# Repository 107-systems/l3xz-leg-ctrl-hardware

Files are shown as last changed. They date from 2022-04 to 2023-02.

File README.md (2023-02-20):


`l3xz-leg-ctrl-hardware`
========================


Custom leg controller board for the [L3X-Z Hexapod](https://github.com/107-systems/l3xz-hw).

<p align="center">
  
</p>

## Firmware
[l3xz-leg-ctrl-firmware](https://github.com/107-systems/l3xz-leg-ctrl-firmware)

## Pin Usage
### Arduino Nano 33 IoT connector CN1
| **Pin** | **Pin Name** | **Signal** | **Description** |
|:---:|:---:|:---:|:---:|
| 1 | D13/SCK | SPI_SCK | SPI for CAN and AS5048 encoder |
| 2 | +3V3 | 3V3-rail | supply voltage for board |
| 3 | AREF | | |
| 4 | DAC0/A0 | | |
| 5 | A1 | +BATT_MEAS | measurement of input voltage |
| 6 | A2 | | |
| 7 | A3 | | |
| 8 | A4/SDA | I2C_SDA | I2C for eeprom and qwiic |
| 9 | A5/SCL | I2C_SCL | I2C for eeprom and qwiic |
| 10 | A6 | LED3 | status LED 3 |
| 11 | A7 | LED2 | status LED 2 |
| 12 | VUSB/+5V0 | | |
| 13 | REC/RESET | RESET | Reset |
| 14 | GND | GND | GND |
| 15 | VIN | power input | power input for board |
| 16 | D1/TX | SERIAL_TX | to connector CN3 |
| 17 | D0/RX | SERIAL_RX | to connector CN3 |
| 18 | RESET | RESET | Reset |
| 19 | GND | GND | GND |
| 20 | D2 | LED1 | status LED 1 |
| 21 | D3 | MCP2515_CS | chip select for CAN |
| 22 | D4 | AS5048_1_CS | chip select for AS5048 1 |
| 23 | D5 | AS5048_2_CS | chip select for AS5048 2 |
| 24 | D6 | BUMPER | input for bumper |
| 25 | D7 | SERVO1 | PWM output for servo 1 |
| 26 | D8 | | |
| 27 | D9 | MCP2515_INT | CAN interrupt |
| 28 | D10 | SERVO2 | PWM output for servo 2 |
| 29 | D11/MOSI | SPI_MOSI | SPI for CAN and AS5048 encoder |
| 30 | D12/MISO | SPI_MISO | SPI for CAN and AS5048 encoder |

### Qwiic I2C connector CN2
JST SH 1mm 4-pin.

| **Pin** | **Signal** |
|:---:|:---:|
| 1 | GND |
| 2 | VCC |
| 3 | I2C_SDA |
| 4 | I2C_SCL |

### Serial connector CN3
JST SH 1mm 4-pin.

| **Pin** | **Signal** |
|:---:|:---:|
| 1 | GND |
| 2 | VCC |
| 3 | SERIAL_TX |
| 4 | SERIAL_RX |

### Dronecode CAN connector CN4 and CN5
JST GH 1.25mm 4-pin.

| **Pin** | **Signal** |
|:---:|:---:|
| 1 | CANVCC |
| 2 | CANH |
| 3 | CANL |
| 4 | GND |

### Power Input CN6
Würth WR-TBL 3.81mm 2-pin.

| **Pin** | **Signal** | **Description** |
|:---:|:---:|:---:|
| 1 | V-IN | Directly to Arduino Nano VIN |
| 2 | GND | |

Attention: V_IN is 5 to 21 V and is directly connected to VIN of the Arduino with a diode for reverse polarity protection.
It is also directly connected to +5V of the servo connector. So it should be limited to +6V if servos are used.

### Cervo connector CN7
2x3 pin-header 2.54 mm.

| **Pin** | **Signal** | **Description** |
|:---:|:---:|:---:|
| 1+2 | servo-pwm | 50 Hz pulse signal |
| 3+4 | +5V | directly connected to VIN |
| 5+6 | GND | |

### Bumper Connector CN8
WAGO 733-362 2.5mm 2-pin.

| **Pin** | **Signal** | **Description** |
|:---:|:---:|:---:|
| 1 | BUMPER | 10k pull up to +3.3V |
| 2 | GND | |

## BOM

| **Designator** | **Part Name** | **Link** |
|:---:|:---:|:---:|
| C1, C2, C3, C4, C5, C6, C9 | Capacitor 0603 100nF 25V  | |
| C7, C8 | do not install | |
| C10, C11 | do not install | |
| CN1 | Arduino Nano | https://www.reichelt.de/praez-buchsenleisten-2-54-mm-1x15-gerade-mpe-115-1-015-p187279.html |
| CN2, CN3 | JST SH SM04B-SRSS-TB | |
| CN4, CN5 | JST GH SM04B-GHS-TB | https://www.voelkner.de/products/1102742/JST-Stiftgehaeuse-Platine-GH-Polzahl-Gesamt-4-Rastermass-1.25mm-SM04B-GHS-TB-LF-SN.html |
| CN6 | Würth WR-TBL 691322310002 | |
| CN7 | Pinheader 2.54 mm 2x3 | https://www.reichelt.de/stiftleisten-2-54-mm-2x03-gewinkelt-mpe-088-2-006-p119904.html |
| CN8 | WAGO 733-362 | https://www.reichelt.de/print-stiftleiste-micro-rm-2-5-gewinkelt-2-pol--wago-733-362-p45863.html |
| D1 | LED 0603 green | https://www.reichelt.de/led-smd-1608-0603-gruen-112-mcd-120--led-el-0603-gr1-p156254.html |
| D2, D3 | MBR0530T1G | https://www.reichelt.de/schottkydiode-30-v-0-5-a-sod-123-mbr0530t1g-ons-p219621.html |
| D4 | LED 0603 yellow | https://www.reichelt.de/led-smd-1608-0603-gelb-180-mcd-120--led-el-0603-ge-p156259.html |
| D5 | LED 0603 red | https://www.reichelt.de/led-smd-1608-0603-rot-180-mcd-120--led-el-0603-rt-p156256.html |
| R1, R2, R3, R4, R6, R7, R8, R9, R10, R14 | Resistor 0603 10k | |
| R5, R15, R16 | Resistor 0603 3k3 | |
| R11, 12 | do not install | |
| R13 | Resistor 0603 100k | |
| U1, U2 | AS5048A | |
| U3 | 24LC64-I/SN | https://www.reichelt.de/eeprom-seriell-64-kb-8-k-x-8-i2c-2-5--5-5-v-so-8-24lc64-i-sn-p40079.html |
| U4 | MCP2515-I/P DIP-18 | https://www.reichelt.de/can-controller-mit-spi-schnittstelle-dil-18-mcp-2515-i-p-p54514.html |
| U8 alternative | MCP2515-I/SO SO-18 | https://www.reichelt.de/can-controller-mit-spi-schnittstelle-2-7--5-5-v-so-18-mcp-2515-i-so-p54515.html |
| U9 | SN65HVD232D | |
| U9 alternative | SN65HVD230D | https://www.reichelt.de/high-speed-can-transceiver-1-mbit-s-3-3-v-so-8-sn-65hvd230d-p58427.html |
| Y1 | Quartz 16 MHz 5x2.5mm | https://www.reichelt.de/keramik-smd-quarz-3x5x1mm-16-0mhz-16-000000-mj-p85005.html |

## PCB
### Top
<p align="center">
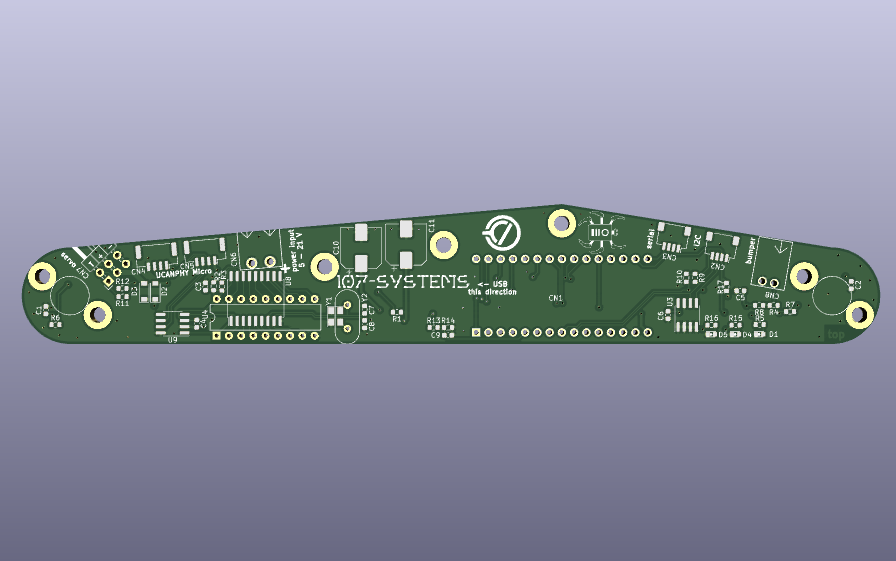
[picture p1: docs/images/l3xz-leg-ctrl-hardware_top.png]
  </a>
</p>
### Bottom
<p align="center">
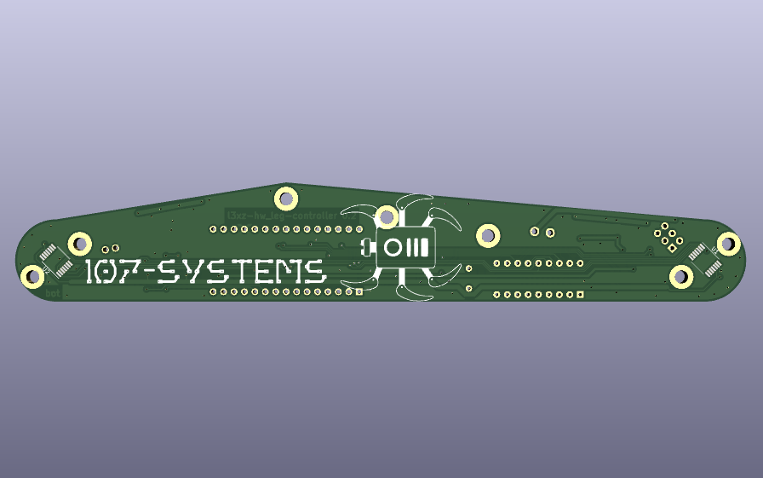
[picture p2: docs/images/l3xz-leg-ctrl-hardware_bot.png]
  </a>
</p>

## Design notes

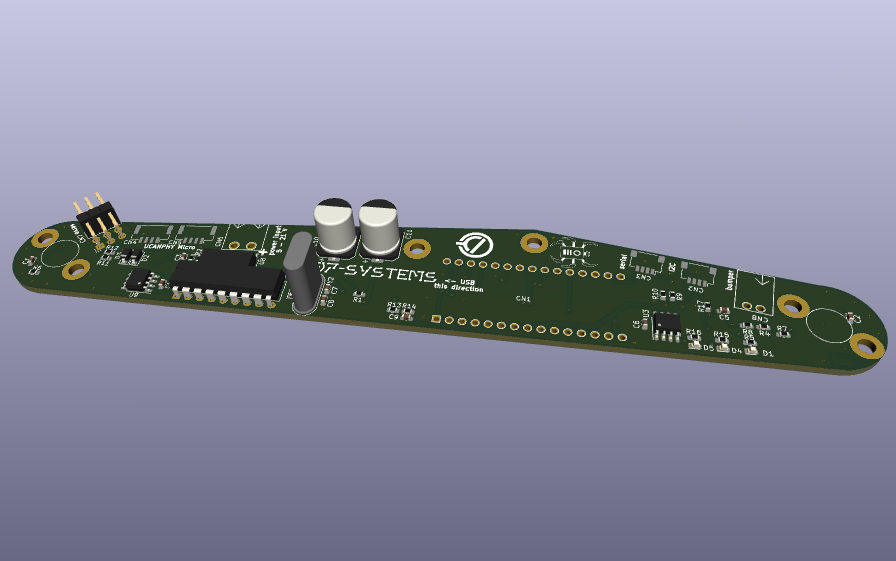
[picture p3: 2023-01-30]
docs/images/l3xz-leg-ctrl-hardware_rendering.png

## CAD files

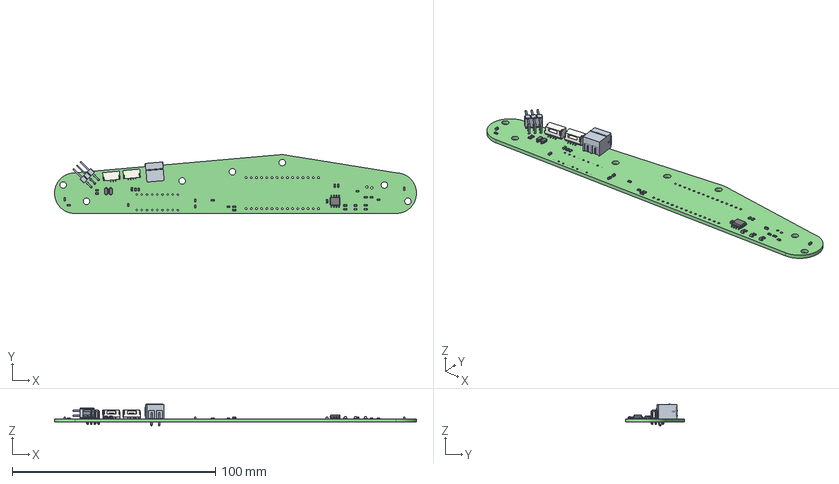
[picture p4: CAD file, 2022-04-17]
l3xz-leg-ctrl-hardware.step
178.0 x 29.0 x 10.7 mm
SOIC-18_7.5x11.6mm_Pitch1.27mm
SOIJ-8_5.3x5.3mm_Pitch1.27mm
c_elec_8x10 x 2

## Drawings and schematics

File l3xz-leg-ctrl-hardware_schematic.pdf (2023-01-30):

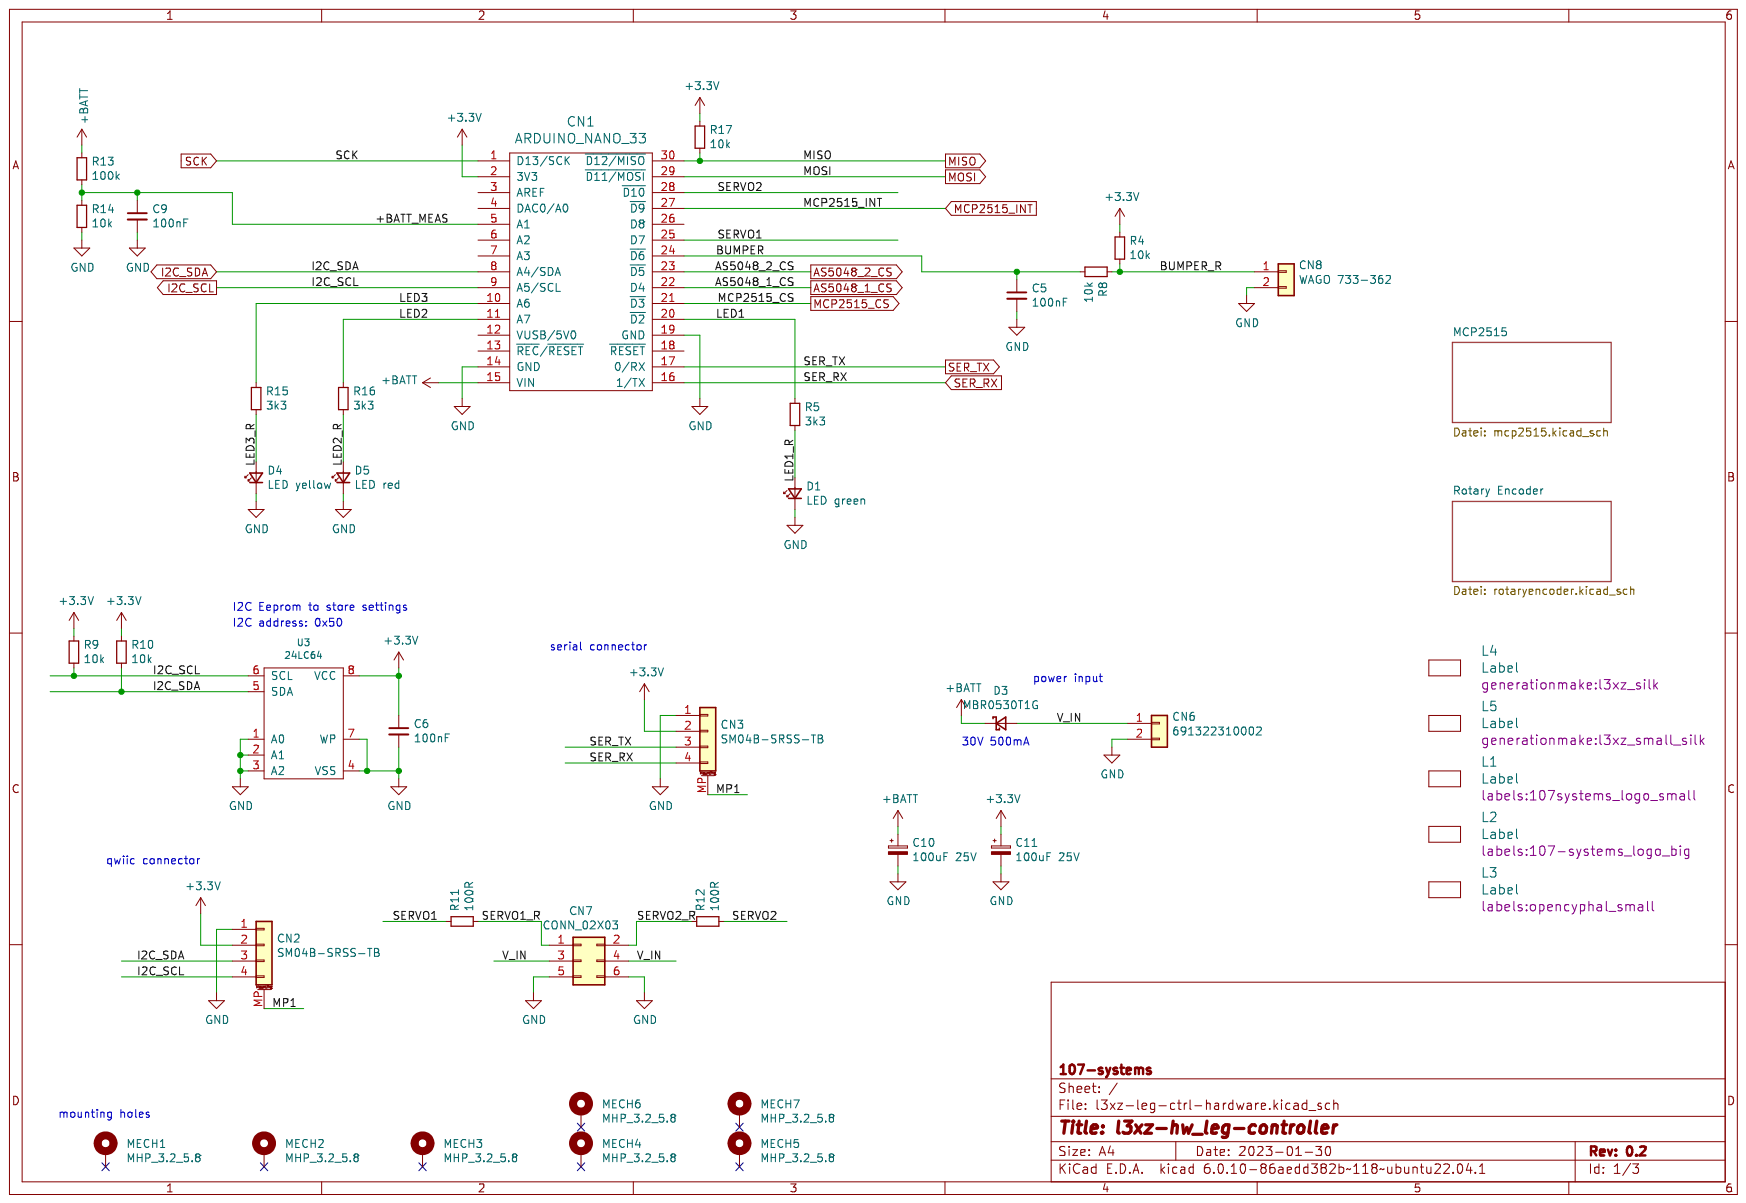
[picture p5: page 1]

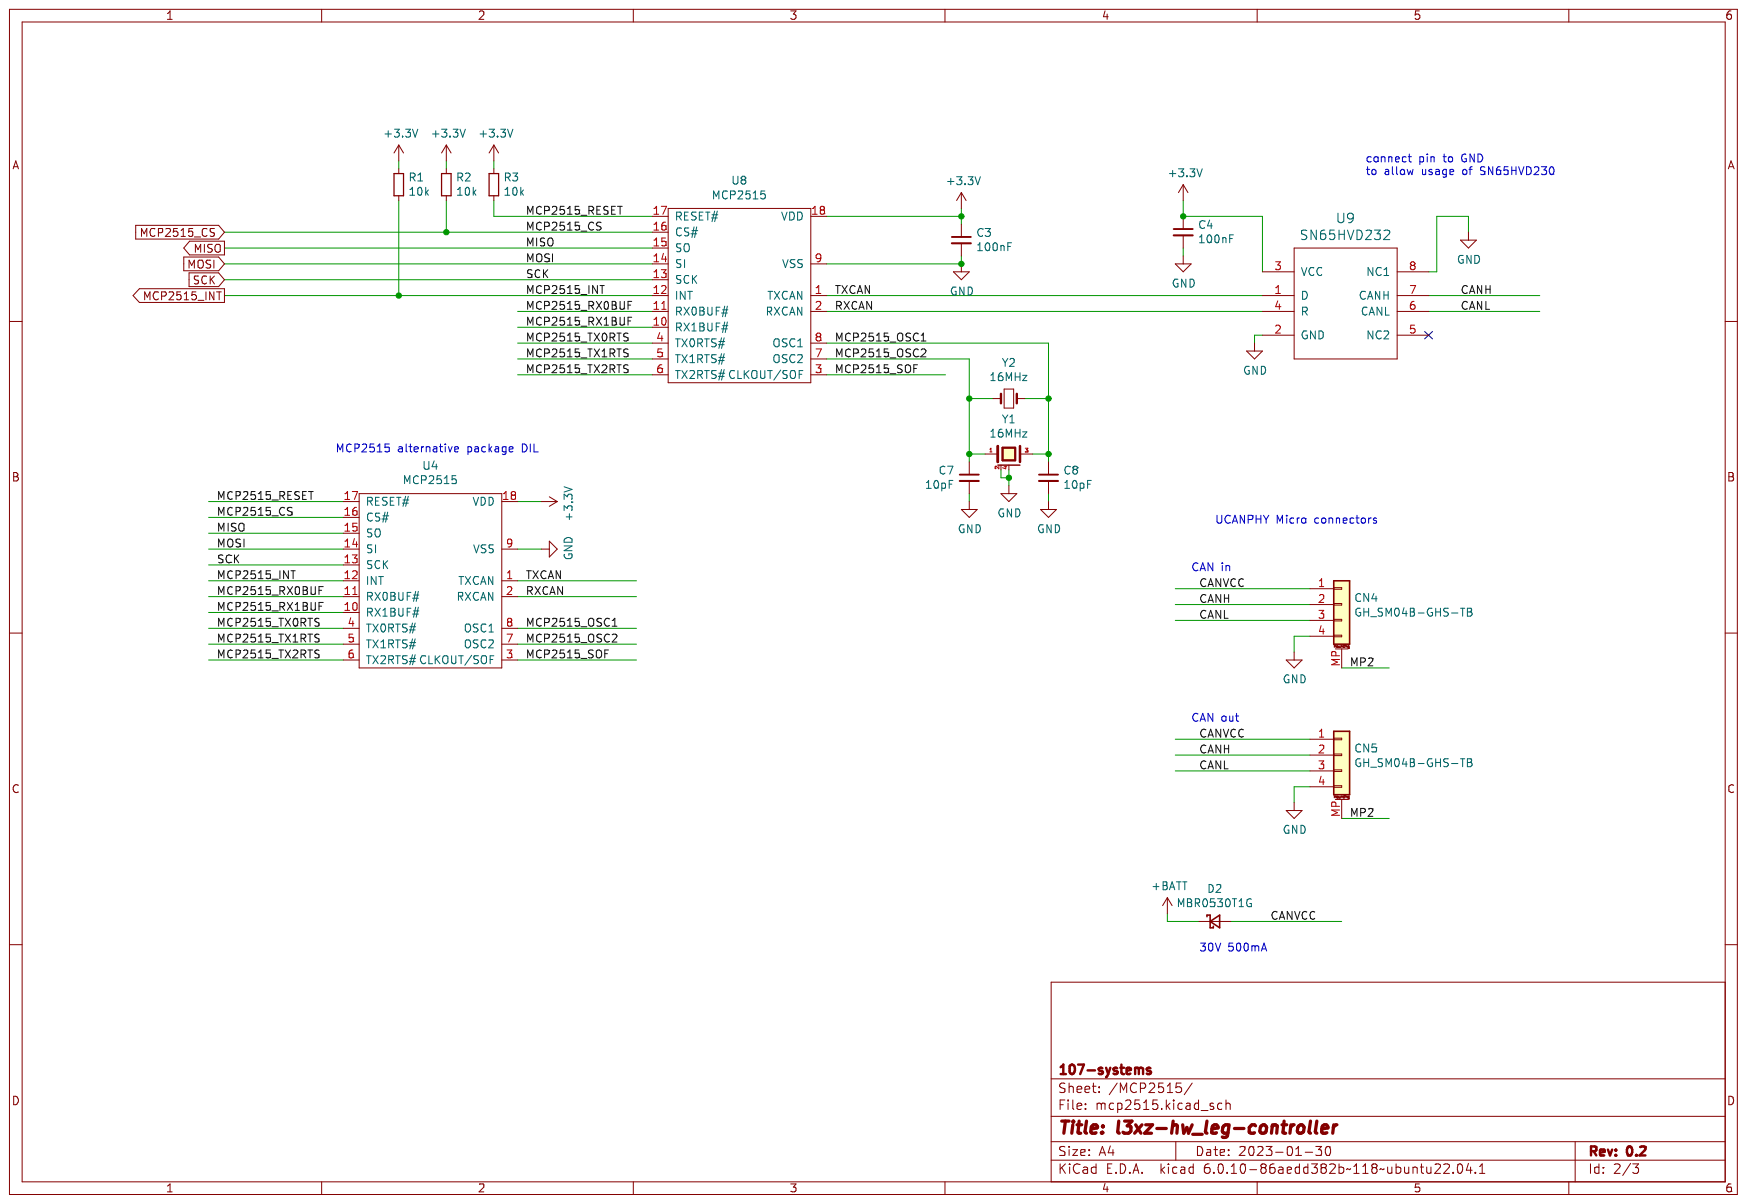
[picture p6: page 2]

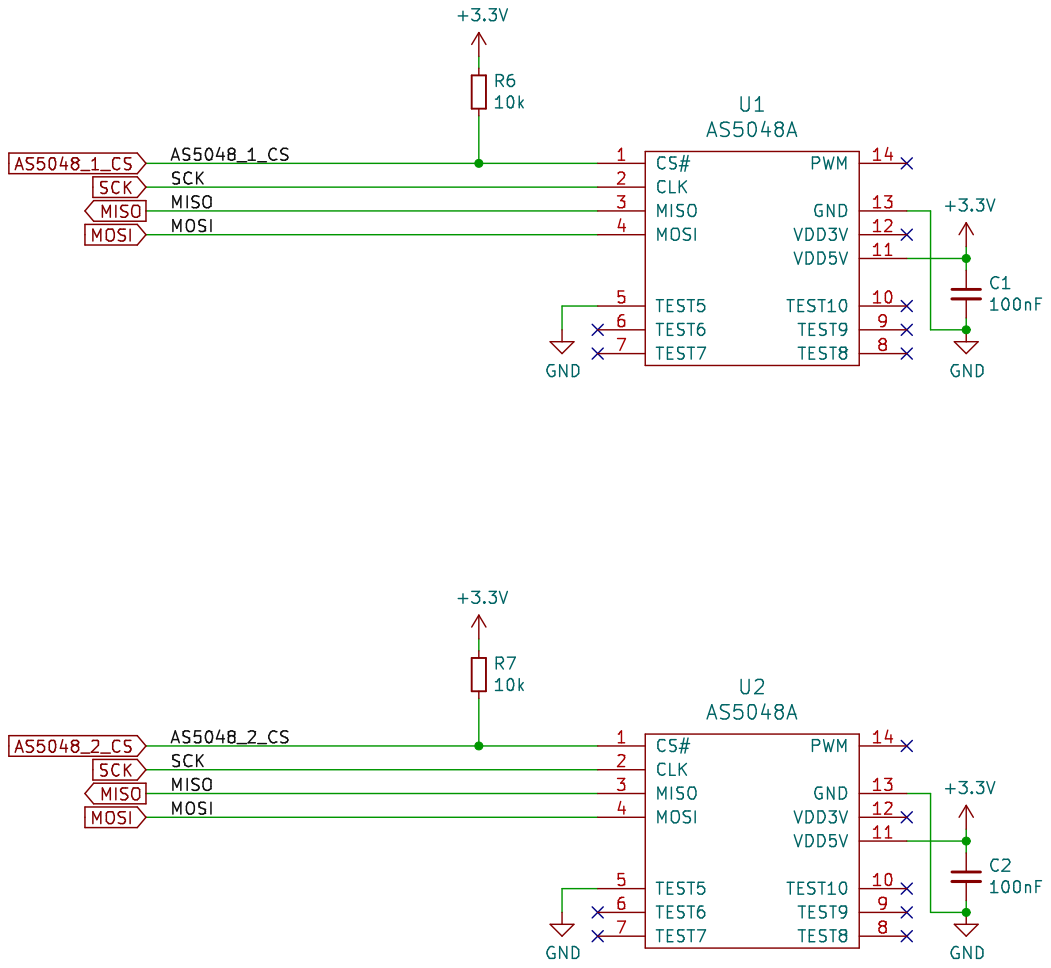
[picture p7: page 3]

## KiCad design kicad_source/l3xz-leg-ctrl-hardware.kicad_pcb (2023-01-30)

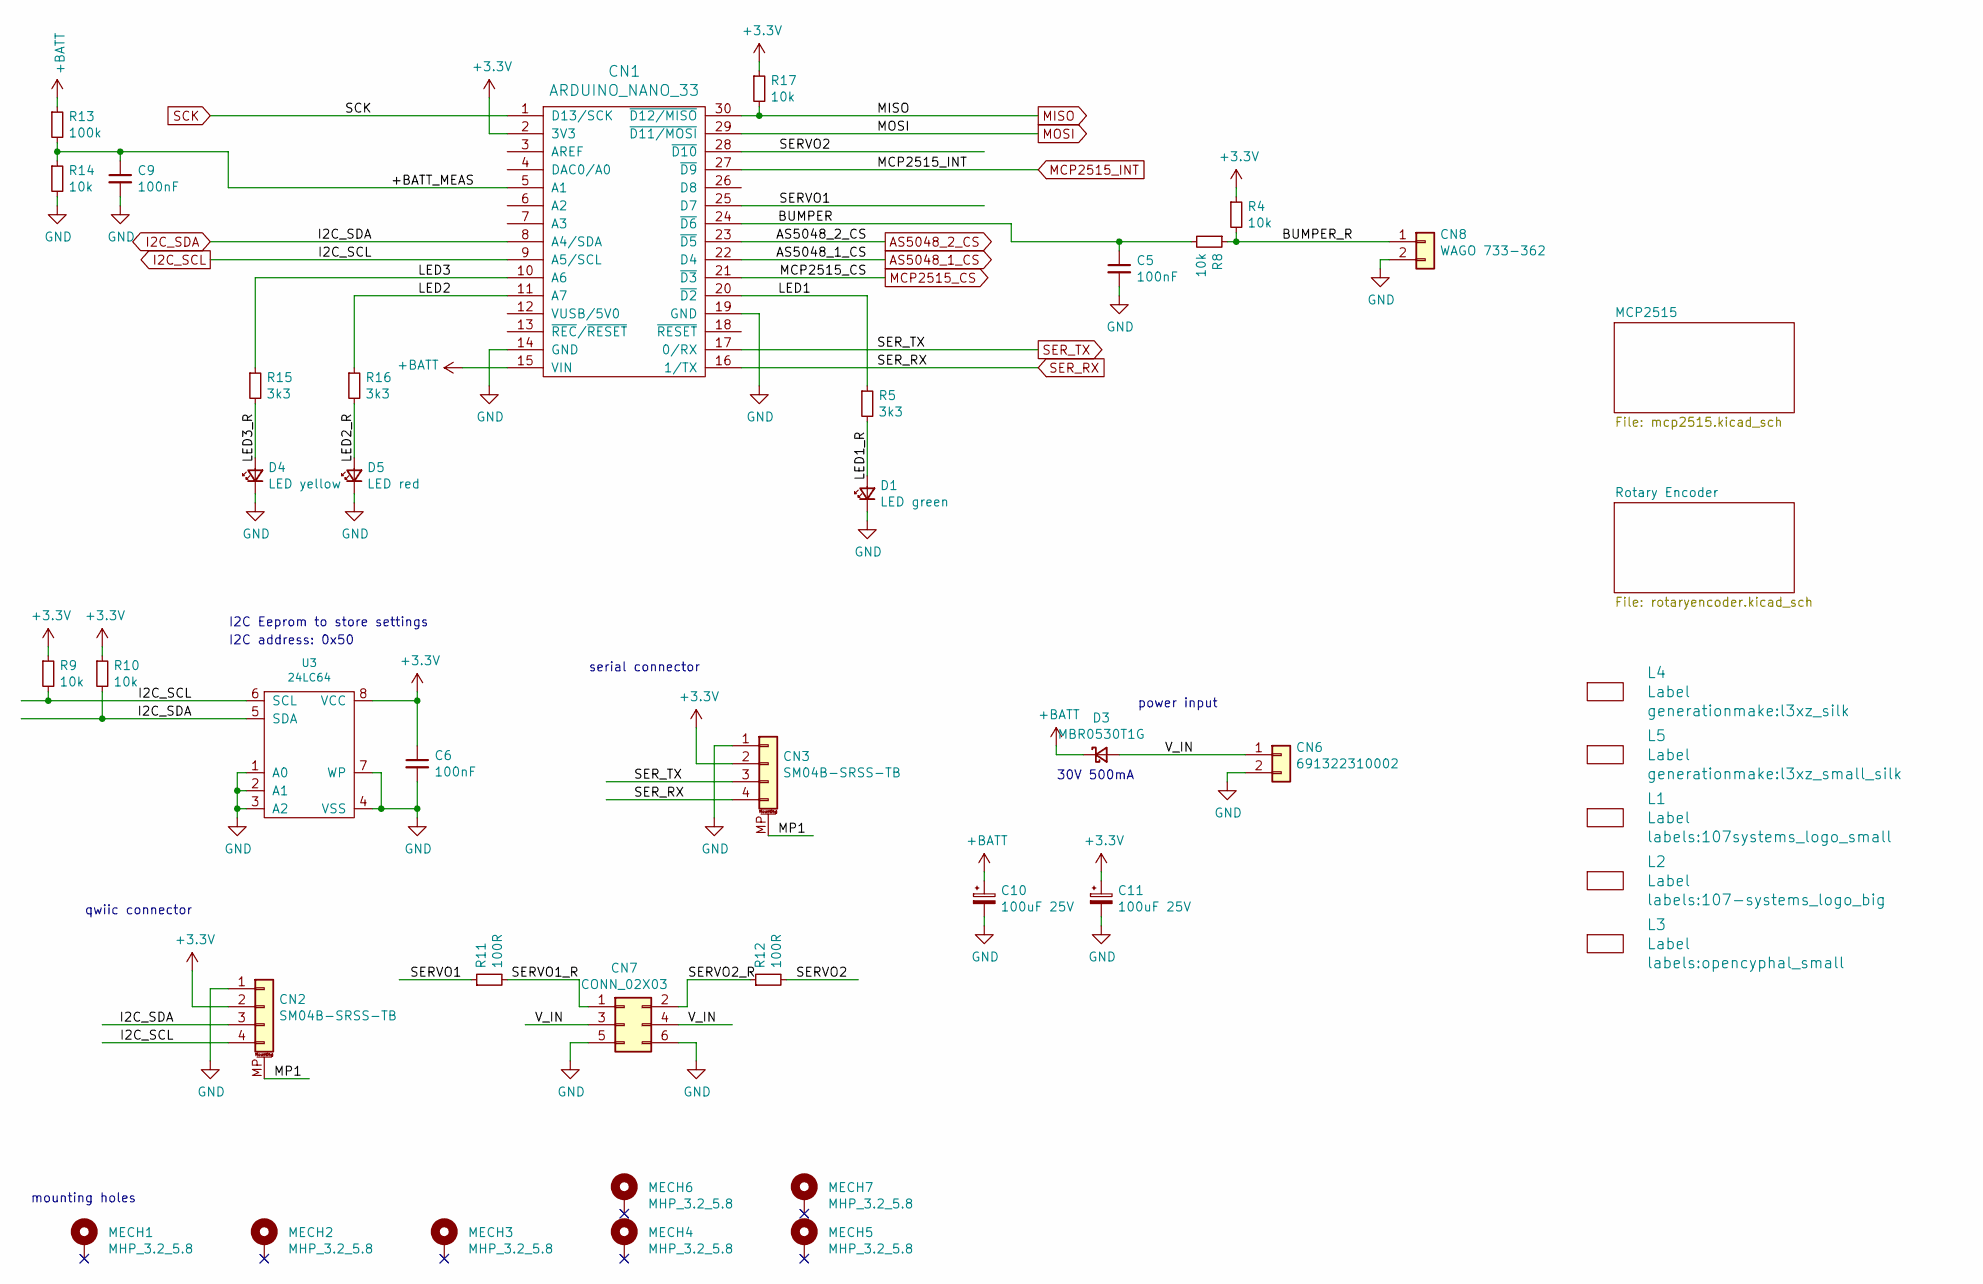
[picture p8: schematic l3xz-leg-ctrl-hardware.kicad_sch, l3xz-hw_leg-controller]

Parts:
C5, C6, C9: 100nF; C_0603_1608Metric
C10, C11: 100uF 25V; CP_Elec_8x10
CN1: ARDUINO_NANO_33
CN2, CN3: SM04B-SRSS-TB; JST_SH_SM04B-SRSS-TB_1x04-1MP_P1.00mm_Horizontal
CN6: 691322310002; WR-TBL_691322310002
CN7: CONN_02X03; PinHeader_2x03_P2.54mm_Horizontal
CN8: WAGO 733-362; WR-TBL_691382010002
D1: LED green; LED_0603
D3: MBR0530T1G; D_SOD-123
D4: LED yellow; LED_0603
D5: LED red; LED_0603
L1: Label; 107systems_logo_small
L2: Label; 107-systems_logo_big
L3: Label; opencyphal_small
L4: Label; l3xz_silk
L5: Label; l3xz_small_silk
MECH1, MECH2, MECH3, MECH4, MECH5, MECH6, MECH7: MHP_3.2_5.8
R4, R8, R9, R10, R14, R17: 10k; R_0603_1608Metric
R5, R15, R16: 3k3; R_0603_1608Metric
R11, R12: 100R; R_0603_1608Metric
R13: 100k; R_0603_1608Metric
U3: 24LC64; SOIC-8_3.9x4.9mm_P1.27mm

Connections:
+3.3V: C6.1, C11.1, CN1.2 (3V3), CN2.2, CN3.2, R4.1, R9.1, R10.1, R17.1, U3.8 (VCC); also elsewhere on the board
+BATT: C10.1, CN1.15 (VIN), D3.1 (K), R13.1; also elsewhere on the board
/+BATT_MEAS: C9.1, CN1.5 (A1), R13.2, R14.1
/BUMPER: C5.1, CN1.24 (~D6), R8.2
/BUMPER_R: CN8.1, R4.2, R8.1
/LED1: CN1.20 (~D2), R5.1
/LED1_R: D1.2 (A), R5.2
/LED2: CN1.11 (A7), R16.1
/LED2_R: D5.2 (A), R16.2
/LED3: CN1.10 (A6), R15.1
/LED3_R: D4.2 (A), R15.2
/MP1: CN2.MP (MountPin), CN3.MP (MountPin)
/SERVO1: CN1.25 (D7), R11.1
/SERVO1_R: CN7.1, R11.2
/SERVO2: CN1.28 (~D10), R12.2
/SERVO2_R: CN7.2, R12.1
/V_IN: CN6.1, CN7.3, CN7.4, D3.2 (A)
AS5048_1_CS: CN1.22 (D4); also elsewhere on the board
AS5048_2_CS: CN1.23 (~D5); also elsewhere on the board
GND: C5.2, C6.2, C9.2, C10.2, C11.2, CN1.14 (GND), CN1.19 (GND), CN2.1, CN3.1, CN6.2, CN7.5, CN7.6, CN8.2, D1.1 (K), D4.1 (K), D5.1 (K), R14.2, U3.1 (A0), U3.2 (A1), U3.3 (A2), U3.4 (VSS), U3.7 (WP); also elsewhere on the board
I2C_SCL: CN1.9 (A5/SCL), CN2.4, R9.2, U3.6 (SCL)
I2C_SDA: CN1.8 (A4/SDA), CN2.3, R10.2, U3.5 (SDA)
MCP2515_CS: CN1.21 (~D3); also elsewhere on the board
MCP2515_INT: CN1.27 (~D9); also elsewhere on the board
MISO: CN1.30 (~D12/MISO), R17.2; also elsewhere on the board
MOSI: CN1.29 (~D11/MOSI); also elsewhere on the board
SCK: CN1.1 (D13/SCK); also elsewhere on the board
SER_RX: CN1.16 (1/TX), CN3.4
SER_TX: CN1.17 (0/RX), CN3.3

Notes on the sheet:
serial connector
power input
I2C address: 0x50
qwiic connector
mounting holes
30V 500mA
I2C Eeprom to store settings

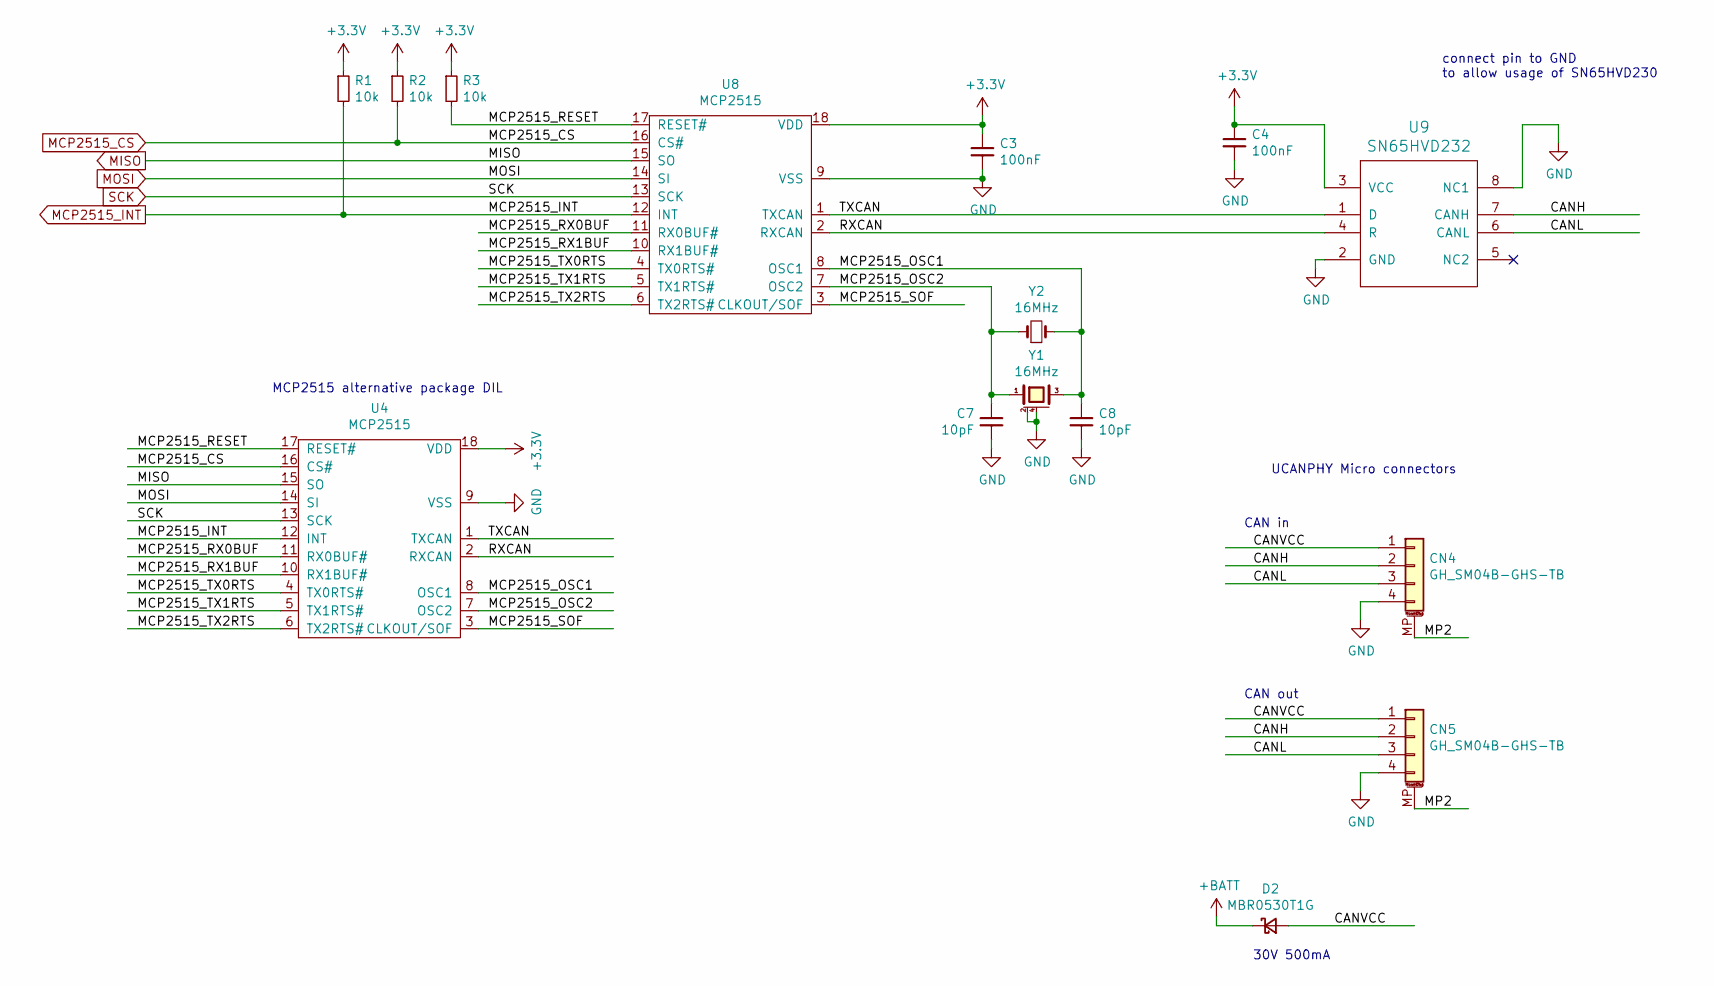
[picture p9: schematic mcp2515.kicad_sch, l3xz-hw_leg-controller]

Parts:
C3, C4: 100nF; C_0603_1608Metric
C7, C8: 10pF; C_0603_1608Metric
CN4, CN5: GH_SM04B-GHS-TB; JST_GH_SM04B-GHS-TB_1x04-1MP_P1.25mm_Horizontal
D2: MBR0530T1G; D_SOD-123
R1, R2, R3: 10k; R_0603_1608Metric
U4: MCP2515; DIP-18_W7.62mm
U8: MCP2515; SOIC-18W_7.5x11.6mm_P1.27mm
U9: SN65HVD232; SOIC-8_3.9x4.9mm_P1.27mm
Y1: 16MHz; Crystal_SMD_SeikoEpson_FA238V-4Pin_3.2x2.5mm
Y2: 16MHz; Crystal_HC49-U_Vertical

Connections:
+3.3V: C3.1, C4.1, R1.1, R2.1, R3.1, U4.18 (VDD), U8.18 (VDD), U9.3 (VCC); also elsewhere on the board
+BATT: D2.1 (K); also elsewhere on the board
/MCP2515/CANH: CN4.2, CN5.2, U9.7 (CANH)
/MCP2515/CANL: CN4.3, CN5.3, U9.6 (CANL)
/MCP2515/CANVCC: CN4.1, CN5.1, D2.2 (A)
/MCP2515/MCP2515_OSC1: C8.1, U4.8 (OSC1), U8.8 (OSC1), Y1.3, Y2.2
/MCP2515/MCP2515_OSC2: C7.1, U4.7 (OSC2), U8.7 (OSC2), Y1.1, Y2.1
/MCP2515/MCP2515_RESET: R3.2, U4.17 (RESET#), U8.17 (RESET#)
/MCP2515/MCP2515_RX0BUF: U4.11 (RX0BUF#), U8.11 (RX0BUF#)
/MCP2515/MCP2515_RX1BUF: U4.10 (RX1BUF#), U8.10 (RX1BUF#)
/MCP2515/MCP2515_SOF: U4.3 (CLKOUT/SOF), U8.3 (CLKOUT/SOF)
/MCP2515/MCP2515_TX0RTS: U4.4 (TX0RTS#), U8.4 (TX0RTS#)
/MCP2515/MCP2515_TX1RTS: U4.5 (TX1RTS#), U8.5 (TX1RTS#)
/MCP2515/MCP2515_TX2RTS: U4.6 (TX2RTS#), U8.6 (TX2RTS#)
/MCP2515/MP2: CN4.MP (MountPin), CN5.MP (MountPin)
/MCP2515/RXCAN: U4.2 (RXCAN), U8.2 (RXCAN), U9.4 (R)
/MCP2515/TXCAN: U4.1 (TXCAN), U8.1 (TXCAN), U9.1 (D)
GND: C3.2, C4.2, C7.2, C8.2, CN4.4, CN5.4, U4.9 (VSS), U8.9 (VSS), U9.2 (GND), U9.8 (NC1), Y1.2 (case), Y1.4 (case); also elsewhere on the board
MCP2515_CS: R2.2, U4.16 (CS#), U8.16 (CS#); also elsewhere on the board
MCP2515_INT: R1.2, U4.12 (INT), U8.12 (INT); also elsewhere on the board
MISO: U4.15 (SO), U8.15 (SO); also elsewhere on the board
MOSI: U4.14 (SI), U8.14 (SI); also elsewhere on the board
SCK: U4.13 (SCK), U8.13 (SCK); also elsewhere on the board

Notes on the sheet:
connect pin to GND to allow usage of SN65HVD230
CAN out
UCANPHY Micro connectors
CAN in
MCP2515 alternative package DIL
30V 500mA

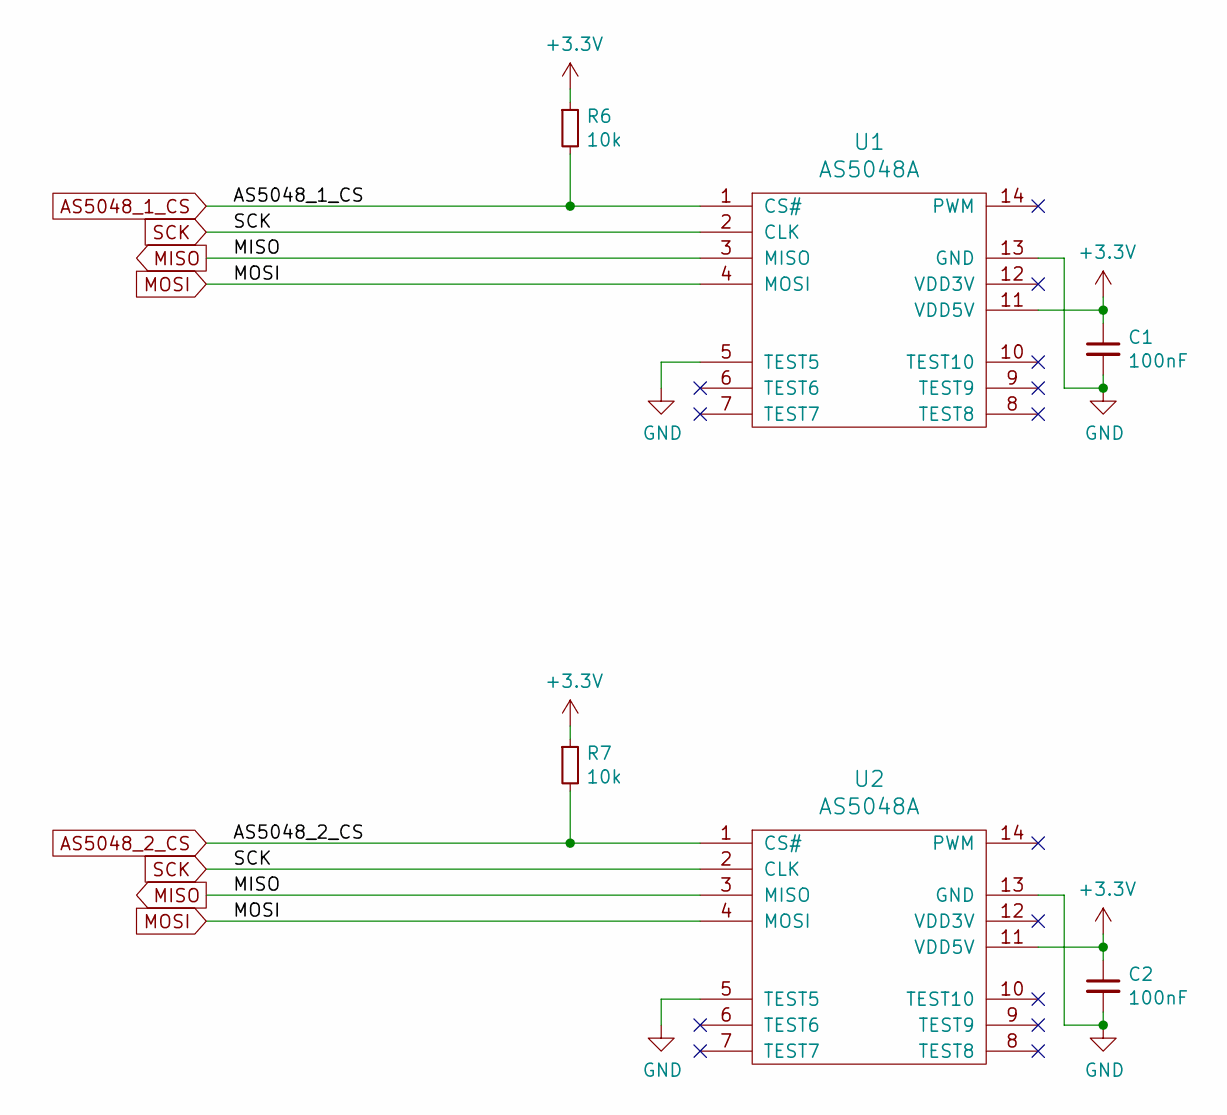
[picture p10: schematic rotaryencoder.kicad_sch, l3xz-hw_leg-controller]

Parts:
C1, C2: 100nF; C_0603_1608Metric
R6, R7: 10k; R_0603_1608Metric
U1, U2: AS5048A; TSSOP-14_4.4x5mm_P0.65mm

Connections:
+3.3V: C1.1, C2.1, R6.1, R7.1, U1.11 (VDD5V), U2.11 (VDD5V); also elsewhere on the board
AS5048_1_CS: R6.2, U1.1 (CS#); also elsewhere on the board
AS5048_2_CS: R7.2, U2.1 (CS#); also elsewhere on the board
GND: C1.2, C2.2, U1.5 (TEST5), U1.13 (GND), U2.5 (TEST5), U2.13 (GND); also elsewhere on the board
MISO: U1.3 (MISO), U2.3 (MISO); also elsewhere on the board
MOSI: U1.4 (MOSI), U2.4 (MOSI); also elsewhere on the board
SCK: U1.2 (CLK), U2.2 (CLK); also elsewhere on the board

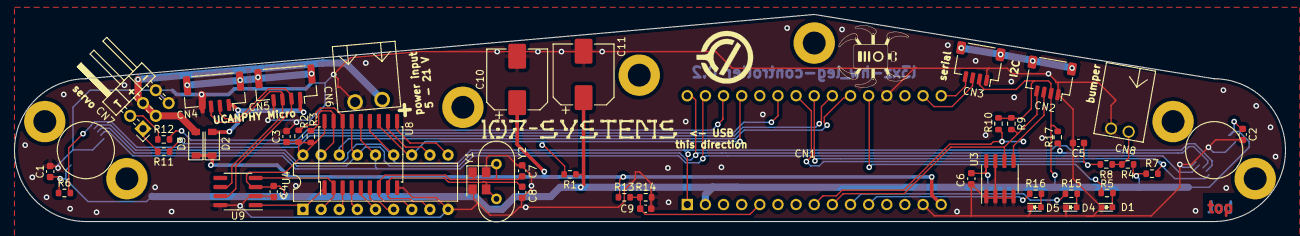
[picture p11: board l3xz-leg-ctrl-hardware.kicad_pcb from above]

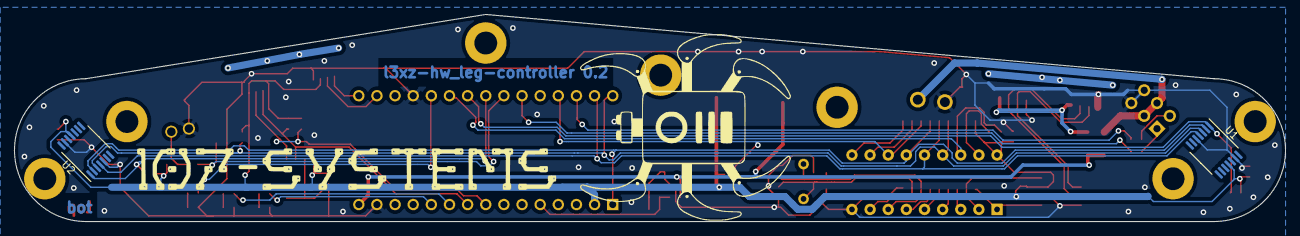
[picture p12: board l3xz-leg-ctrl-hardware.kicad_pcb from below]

Board: 2 copper layers, 178.0 x 29.0 mm, 61 parts (4 on the bottom side), 44 nets.

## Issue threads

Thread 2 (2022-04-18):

fix MCP2515_INT

generationmake, 2022-04-18:
### :bug: Bug Report

<p align="center">
  <a href="https://github.com/107-systems/107-Arduino-Viper">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</a>
</p>

**Describe the bug**

we somehow managed to connect MCP2515_INT to a pin which is not capable of interrupts.

aentinger, 2022-10-11:
That should not be oO. Ive checked ArduinoCore-samd Ehen reviewing the schematic and I remember it was a PCINT pin. Will double-check ...
________________________________
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

Closed 2023-01-30.

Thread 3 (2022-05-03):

mark direction of Arduino Nano

generationmake, 2022-05-03:
### ⚡ Feature Request

<p align="center">
  <a href="https://github.com/107-systems/107-Arduino-Viper">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</a>
</p>

**Please Describe The Problem To Be Solved**
The user does not know how to insert the Arduino Nano correctly. So add a marking in which direction the USB connector has to point.

Closed 2023-01-30.

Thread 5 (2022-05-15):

improvements for next release

generationmake, 2022-05-15:
### ⚡ Feature Request

<p align="center">
  <a href="https://github.com/107-systems/107-Arduino-Viper">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</a>
</p>

In this issue I want to collect all improvements for the next revision of the board.

Closed 2023-01-30.

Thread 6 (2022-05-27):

Use FD-CAN instead of CAN for data communication

aentinger, 2022-05-27:
### ⚡ Feature Request

<p align="center">
  <a href="https://github.com/107-systems/107-Arduino-Viper">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</a>
</p>

**Please Describe The Problem To Be Solved**
Using FD-CAN allows up to 64-Bytes of data per frame leading to less overall frames.

**Suggest A Solution**
Replace the MCP2515 with a MCP2518.

aentinger, 2023-01-25:
Or maybe we go directly 10BASE-T1S. I'm closing this for now.

Closed 2023-01-25.

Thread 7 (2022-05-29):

use of OpenCyphal logos and labels

generationmake, 2022-05-29:
### ⚡ Feature Request

<p align="center">
  <a href="https://github.com/107-systems/107-Arduino-Viper">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</a>
</p>

clarify use of OpenCyphal logos and labels.

Closed 2023-01-30.

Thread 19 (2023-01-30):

move rotary encoders to top side

generationmake, 2023-01-30:
<a href="https://107-systems.org/">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</a>

### ⚡ Feature Request

move rotary encoders to top side to simplify manufacturing. sensitivity should also be given through PCB.

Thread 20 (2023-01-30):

[Feature Request] Replace Arduino Nano 33 IoT with Raspberry Pi Pico

aentinger, 2023-01-30:
<a href="https://107-systems.org/">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</a>

### ⚡ Feature Request

Reasons are both costs and software support (no C++17 on ArduinoCore-samd).

generationmake, 2023-01-30:
and direct solder without stand offs.
if possible because of USB connector.

aentinger, 2023-01-30:
>and direct solder without stand offs.
>if possible because of USB connector.

Full agreement!

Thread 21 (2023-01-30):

[Feature Request] Use much smaller connector for bumper switch (CN8)

aentinger, 2023-01-30:
<a href="https://107-systems.org/">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</a>

### ⚡ Feature Request

Could be a [SM02B-GHS-TB](https://www.digikey.com/en/products/detail/jst-sales-america-inc/SM02B-GHS-TB-LF-SN/807786).

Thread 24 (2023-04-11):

[Feature Request] Use different SPI for MCP2515 and AS5084A

aentinger, 2023-04-11:
<a href="https://107-systems.org/">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</a>

### ⚡ Feature Request

The RP2040 (on the Raspberry Pi Pico) exposes two (2!) SPI interfaces. This allows of separation of the SPI between MCP2515 and AS5084A which are currently shared, which can lead to bottlenecks in the communication.

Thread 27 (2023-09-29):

[Feature Request]

aentinger, 2023-09-29:
<a href="https://107-systems.org/">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</a>

### ⚡ Feature Request

Route CAN / 4-Pin JST GH to the end of the PCB in order to allow connection of a smart footpoint end sensor (could be a 3-dimensional force sensor in the future).

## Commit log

2022-04-03 added first draft of pcb
    [l3xz-hw_leg-controller.kicad_pcb, l3xz-hw_leg-controller.sch, mcp2515.sch]
2022-04-03 added step file
    [l3xz-hw_leg-controller.step]
2022-04-03 added rotary encoder, led and switch
    [l3xz-hw_leg-controller.kicad_pcb, l3xz-hw_leg-controller.sch, mcp2515.sch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]
2022-04-03 added schematic pdf
2022-04-07 added dronecode can and qwiic connectors
    [l3xz-hw_leg-controller.sch, mcp2515.sch]
2022-04-07 added eeprom and servo connectors, updated pdf
    [l3xz-hw_leg-controller.sch, mcp2515.sch]
2022-04-08 updated schematic, corrected connector designators, updated footprints
    [l3xz-hw_leg-controller.sch, mcp2515.sch, rotaryencoder.sch]
2022-04-08 made first draft for layout
    [l3xz-hw_leg-controller.kicad_pcb]
2022-04-08 added pull up to i2c, serial resistor to servo
    [l3xz-hw_leg-controller.kicad_pcb, l3xz-hw_leg-controller.sch]
2022-04-10 updated connectors, added power input
    [l3xz-hw_leg-controller.kicad_pcb, l3xz-hw_leg-controller.sch, mcp2515.sch]
2022-04-10 added additional leds, input measurement buffer capacitors
    [l3xz-hw_leg-controller.kicad_pcb, l3xz-hw_leg-controller.sch]
2022-04-10 added labels, beautified layout
    [l3xz-hw_leg-controller.kicad_pcb, l3xz-hw_leg-controller.sch, mcp2515.sch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]
2022-04-10 updated schematic pdf and images
2022-04-12 added alternative DIL package for MCP2515
    [l3xz-hw_leg-controller.kicad_pcb, l3xz-hw_leg-controller.sch, mcp2515.sch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]
2022-04-17 updated step model, added link to software in readme
    [l3xz-hw_leg-controller.step]
2022-05-03 added BOM to readme
2022-05-08 updated some part values
    [l3xz-hw_leg-controller.sch]
2022-05-29 updated BOM in readme and schematic, updated schematic pdf
    [l3xz-hw_leg-controller.sch, mcp2515.sch]
2022-05-29 exchanged pin D7 and D9 and connected U9, pin8 to GND in readme and schematic as all boards have been reworked
    [l3xz-hw_leg-controller.sch, mcp2515.sch]
2022-06-05 fixed MCP2515_INT and direction label for Arduino
    [l3xz-hw_leg-controller.kicad_pcb, l3xz-hw_leg-controller.sch, mcp2515.sch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]
2022-06-05 fixed crystal issues, corrected CAN driver footprint, added pullup on MISO
    [l3xz-hw_leg-controller.kicad_pcb, l3xz-hw_leg-controller.sch, mcp2515.sch]
2022-06-05 updated images and schematic pdf
    [l3xz-hw_leg-controller.kicad_pcb, mcp2515.sch]
2023-01-25 Rename repository to l3xz-leg-ctrl-hardware. (#18)
    [l3xz-leg-ctrl-hardware.kicad_pcb, l3xz-leg-ctrl-hardware.sch, l3xz-leg-ctrl-hardware.step]
2023-01-25 updated project to kicad 6
    [l3xz-leg-ctrl-hardware.kicad_sch, mcp2515.kicad_sch, rotaryencoder.kicad_sch]
2023-01-25 updated some symbol library links
    [l3xz-leg-ctrl-hardware.kicad_sch, mcp2515.kicad_sch, rotaryencoder.kicad_sch]
2023-01-29 updated footprint library
    [l3xz-leg-ctrl-hardware.kicad_pcb, l3xz-leg-ctrl-hardware.kicad_sch, mcp2515.kicad_sch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]
2023-01-29 connected mounting pads of connectors
    [l3xz-leg-ctrl-hardware.kicad_pcb, l3xz-leg-ctrl-hardware.kicad_sch, mcp2515.kicad_sch]
2023-01-30 fixed drc errors
    [l3xz-leg-ctrl-hardware.kicad_pcb, l3xz-leg-ctrl-hardware.kicad_sch, mcp2515.kicad_sch]
2023-01-30 added labels, updated pdf schematic and images
    [l3xz-leg-ctrl-hardware.kicad_pcb, l3xz-leg-ctrl-hardware.kicad_sch, mcp2515.kicad_sch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]
2023-02-20 Add CI workflow to check for commonly misspelled words (#23)
    On every push, pull request, and periodically, use codespell to check for commonly
    misspelled words.
    In the event of a false positive, the problematic word should be added, in all lowercase, to the
    field of . Regardless of the case of the word in the false positive, it must be in all lowercase in the
    ignore list. The ignore list is comma-separated with no spaces.
